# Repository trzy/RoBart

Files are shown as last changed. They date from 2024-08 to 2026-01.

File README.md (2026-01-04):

# RoBart: Autonomous LLM-controlled robot using iPhone
*Copyright 2024-2026 Bart Trzynadlowski*

**What if you could put your brain in a robot body?** Okay, okay, that's not possible, but what if you could put Claude or GPT-4 in a robot body? And not just any robot body but a robot body based on a salvaged hoverboard and an iPhone Pro for compute and sensors? That's exactly what I did. Read on, human!

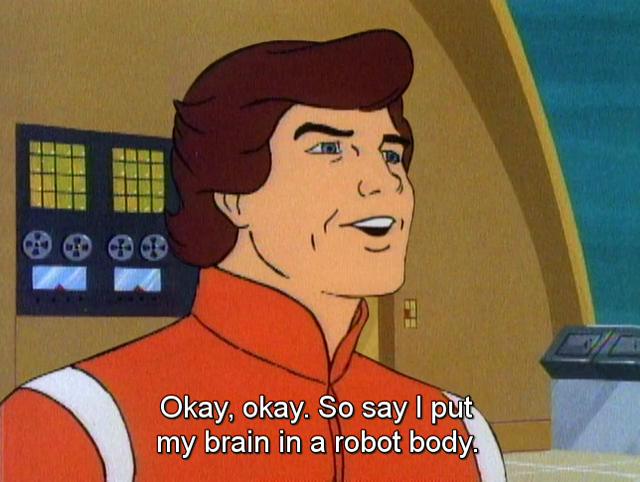
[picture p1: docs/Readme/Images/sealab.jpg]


<table align="center">
  <tr>
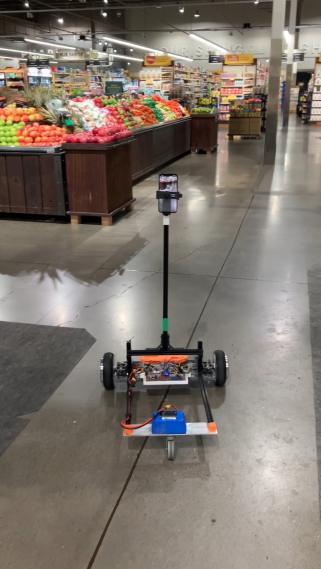
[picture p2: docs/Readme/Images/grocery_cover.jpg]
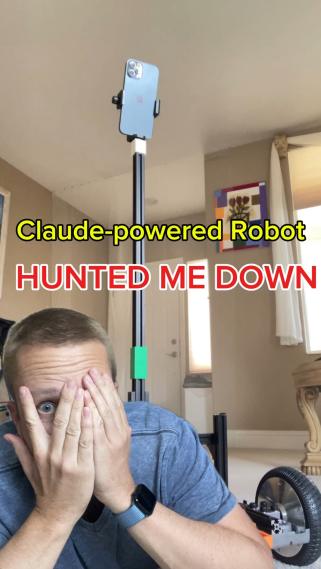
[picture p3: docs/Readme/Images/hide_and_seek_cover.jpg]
    <td align="center"></td> <td align="center"></td>
  </tr>
  <tr>
    <td align="center"><a href="https://www.youtube.com/watch?v=-iW3Vzzr3oU">Grocery shopping</a></td> <td align="center"><a href="https://www.youtube.com/shorts/hnw6pvyZSns">Hide and seek</a></td>
  </tr>
</table>

## Update: January 2026

A teleoperation system using WebRTC and a web client is available for RoBart in [the webrtc-teleop branch](https://github.com/trzy/RoBart/tree/webrtc-teleop).

<table align="center">
  <tr>
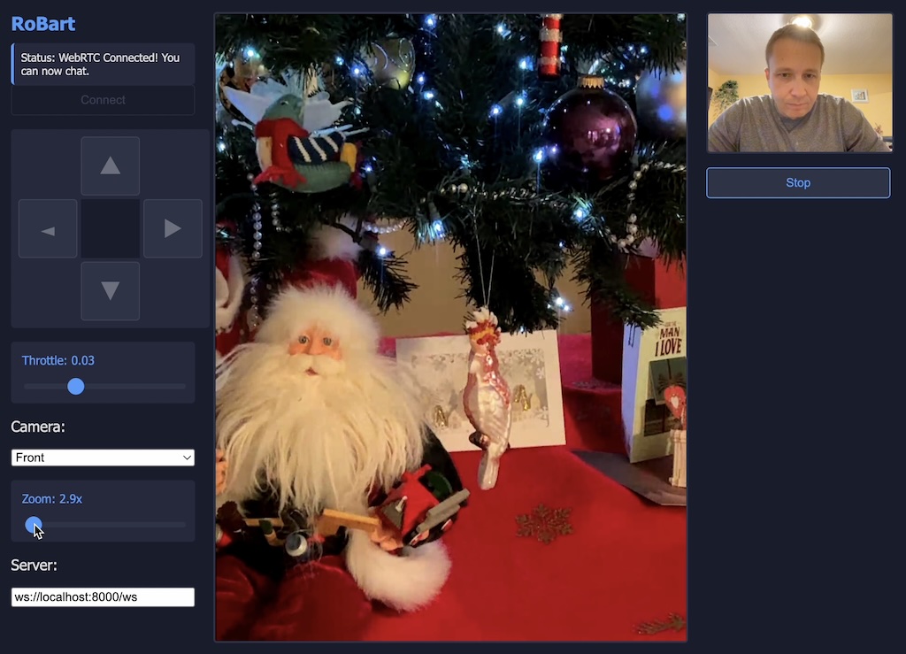
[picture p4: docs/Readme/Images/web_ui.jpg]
    <td align="center"></td>
  </tr>
  <tr>
    <td align="center">Teleoperation interface.</td>
  </tr>
</table>

## Objectives

RoBart began as an attempt to build a cheap mobile base using a hoverboard and iPhone Pro. Mobile phones are easy to work with and provide plenty of compute, connectivity, and useful peripherals: RGB cameras, LiDAR, microphones, speakers. Using [ARKit](https://developer.apple.com/augmented-reality/arkit/), we get SLAM, scene understanding, spatial meshing, and more. Let's see what we can do with this!

I'm open sourcing this project to stimulate discussion and encourage exploration. Some topics to consider:

- **Navigation:** RoBart needs better motion planning and navigation, particularly in household environments. An initial step would be to build a proper [nav mesh](https://en.wikipedia.org/wiki/Navigation_mesh) from its occupancy maps. Proper motion planning would be next.
- **Agent:** The agent could easily be improved with better planning, long-term memory, and spatial awareness. [Vision fine-tuning with GPT-4o](https://openai.com/index/introducing-vision-to-the-fine-tuning-api/) opens up all sorts of exciting possibilities.
- **Mechanical Design:** The mechanical design is a one-off. Can we design a simpler robot that's easier to replicate entirely from off-the-shelf and 3D-printed parts? Virtually nothing would need changing in the code.
- **Manipulation:** A RoBart Mk II should include an end effector, maybe something like this [5-dof Waveshare arm](https://www.waveshare.com/roarm-m1.htm) or the [SO-ARM100](https://github.com/TheRobotStudio/SO-ARM100).
- **Applications:** Accessibility? Tidying-up? Contactless health? Home inspection and security? A robotic porter? What are some fun ideas that could be built?

If you have ideas or contributions, I encourage you to reach out!

<table align="center">
  <tr>
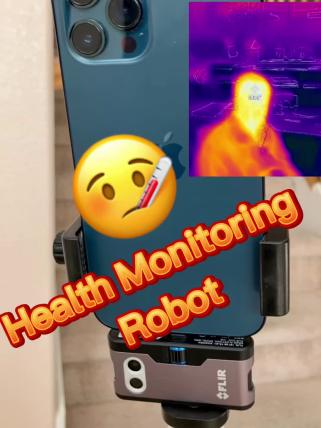
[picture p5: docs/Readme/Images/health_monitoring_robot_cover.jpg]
    <td align="center"></td>
  </tr>
  <tr>
    <td align="center"><a href="https://youtube.com/shorts/GWkYCer5hi8">Contactless health monitoring.</a> Source code for this prototype is not included in this repo.</td>
  </tr>
</table>

## System Architecture

RoBart is a bit of a fever dream of ideas, many only partly finished. I'll attempt to describe how the code base works here.

### High-Level Overview

The RoBart code base contains four distinct applications, only two of which constitute the robot:

1. **iOS application:** This is the main RoBart app that runs on iPhone and controls RoBart. It does not rely on a companion server and makes calls to public LLM APIs directly. The app actually has two modes: robot and handheld, the latter localizing itself to the same SLAM map and allowing for remote control. Located in `ios/RoBart/`.
2. **Arduino firmware:** Firmware that runs on the [Adafruit Feather nRF52 Bluefruit LE](https://www.adafruit.com/product/3406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) to control the motors. Communicates with the iOS app via Bluetooth Low Energy. Located in `hoverboard/`.
3. **watchOS application:** An optional Apple Watch app that allows voice commands to be issued from Watch. This is useful in noisy environments that confound the VAD running on the iPhone. Located in `ios/RoBart/RoBart Remote Control Watch App/` as a watchOS build target.
4. **Debug server:** A Python-based server that the iOS app will attempt to connect to. Provides an interactive terminal that allows various debug commands to be issued, both to control the robot and request data from it. This is not required to operate the robot. Located in `server/`.

The main components of the RoBart iOS app are shown in the diagram below.

<table align="center">
  <tr>
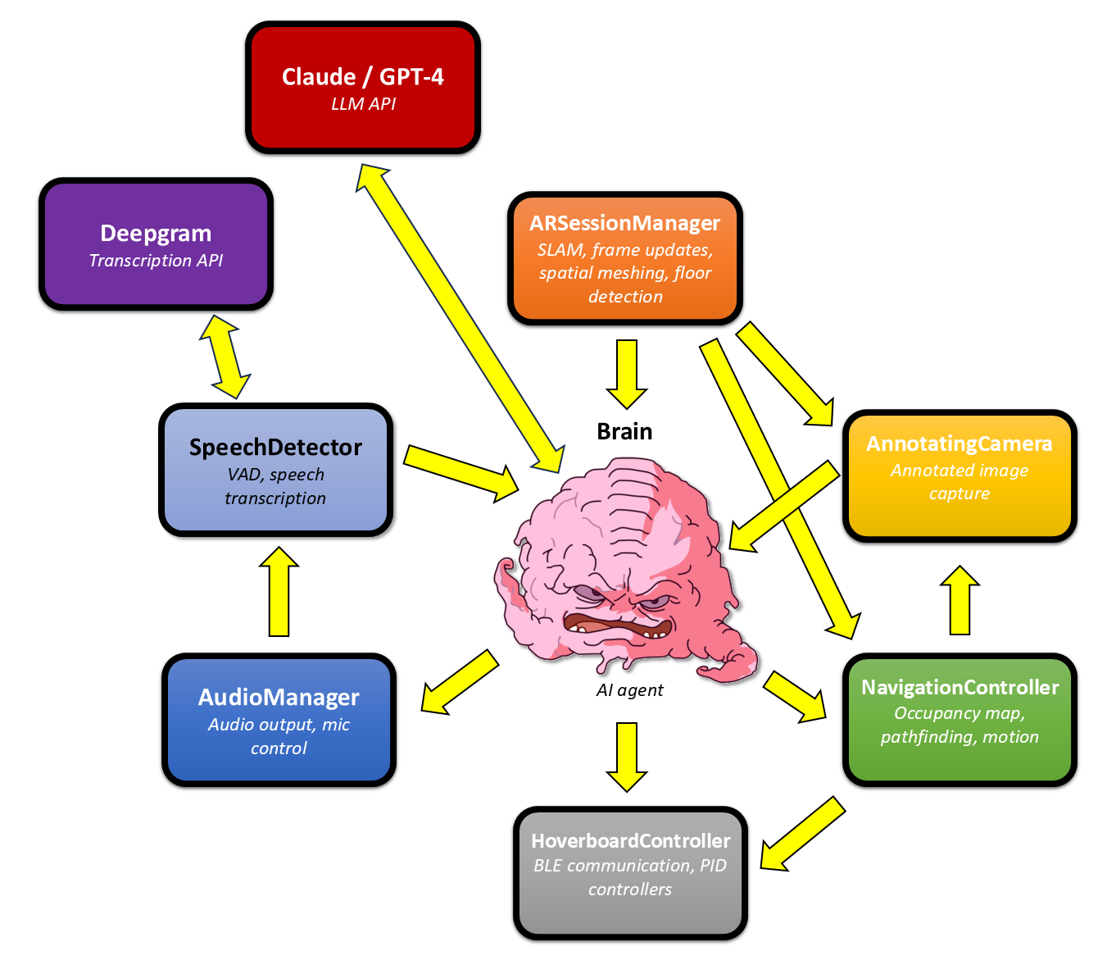
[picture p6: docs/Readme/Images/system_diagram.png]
    <td align="center"></td>
  </tr>
  <tr>
    <td align="center">RoBart iOS app architecture.</td>
  </tr>
</table>

The components are:

- **ARSessionManager:** Using ARKit, publishes camera transform and frame updates, performs scene meshing and floor plane detection, and even supports collaborative sessions with other phones running the app in handheld mode. RoBart components frequently poll the current camera transform or wait for the next frame.
- **SpeechDetector:** Listens for spoken audio, transcribes it using Deepgram, and then publishes the resulting transcript. An external transcription API is used because iOS's `SFSpeechRecognizer` is performance intensive.
- **AudioManager:** Plays audio samples (i.e., RoBart's spoken utterances) and controls the microphone (used by `SpeechDetector`).
- **HoverboardController:** Executes trajectories (e.g., rotate N degrees, drive forward N meters) using PID control on iOS and by sending motor throttle commands to the hoverboard Arduino firmware via BLE.
- **NavigationController:** Higher-level motion control and navigation. Builds an occupancy map, performs very crude pathfinding, provides a nearest-human following task, and executes motion tasks using `HoverboardController`.
- **AnnotatingCamera:** Takes photos and annotates them with navigable points (using the occupancy map). This allows the AI agent to reason about where it can move.
- **Brain:** The AI agent that runs RoBart. Listens for speech and will then attempt to complete the requested task using all of RoBart's capabilities and the chosen LLM.

### Motor Control

`HoverboardController` communicates with the Arduino firmware via BLE. It sends individual motor throttle values (ranging from -1.0 to +1.0, with sign indicating direction) directly. A number of basic trajectory commands are handled on iOS by employing a PID controller that uses ARKit's 6dof pose for feedback (yes, running a PID loop like this through BLE and with ARKit's latency is engineering malpractice but it almost works). These include:

- **drive:** Sets the individual throttle values for the left and right motors, open loop.
- **rotateInPlace:** Turns in place with the given angular velocity (-1 being left at full throttle and +1 being right at full throttle), open loop.
- **rotateInPlaceBy:** Rotates in place by a specified number of degrees.
- **face:** Turns in place to face the given world space direction vector.
- **driveForward:** Drive forward by the specified distance in meters.
- **driveTo:** Drives to the specified world space position in a straight line, both turning to face the point and moving towards it.
- **driveToFacing:** Drives to the specified position while facing the given direction. Particularly useful for driving backwards to a point.

<table align="center">
  <tr>
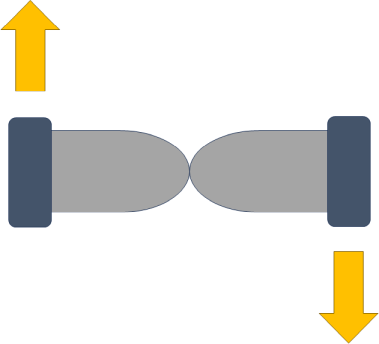
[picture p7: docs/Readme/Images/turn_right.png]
    <td align="center"></td>
  </tr>
  <tr>
    <td align="center">Schematic top-down view of the hoverboard. Rotating right can be accomplished with multiple commands, e.g., <b>drive(leftThrottle: 1, rightThrottle: -1)</b>.</td>
  </tr>
</table>

There is currently no feedback on the Arduino side. No encoder is present on the motors. A watchdog mechanism exists that will cut motor power when either the BLE connection is lost or if motor throttle values are not updated within a certain number of seconds. In the PID controlled modes, a stream of constant updates is sent, which prevents the watchdog from engaging. 

### Position Tracking and Mapping with ARKit

[ARKit](https://developer.apple.com/augmented-reality/arkit/) provides [SLAM](https://en.wikipedia.org/wiki/Simultaneous_localization_and_mapping) for 6dof position and a slew of other useful perception capabilities. The `ARSessionManager` singleton, found in `ios/RoBart/RoBart/AR/ARSessionManager.swift`,
handles the AR session and exposes various useful properties. [RealityKit](https://developer.apple.com/documentation/realitykit) is used for debug rendering of meshes and planes. The AR session is initiated from the AR view container in `ios/RoBart/RoBart/Views/AR/ARViewContainer.swift`

For collision avoidance, RoBart constructs an occupancy map. This is a regular 2D grid on the xz-plane indicating cells that contain world geometry. It is computed by taking all of the vertices produced by scene meshing (see [`ARMeshAnchor`](https://developer.apple.com/documentation/arkit/armeshanchor)) and using a [Metal](https://developer.apple.com/metal/) compute shader to project them onto a 2D grid. The resulting map is used to test for obstructions and plot paths. The occupancy map code is found in `ios/RoBart/RoBart/Navigation/Mapping/`. In order to build it, RoBart needs to know the floor height (i.e., its world space y component) because the occupancy map is computed by looking for obstacles that are within a certain height range above the floor.

<table align="center">
  <tr>
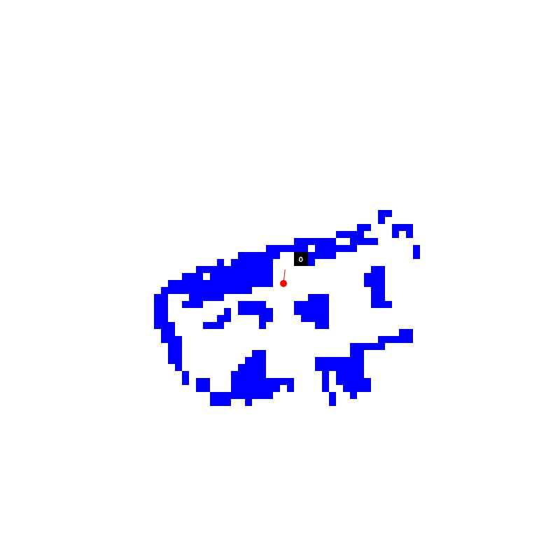
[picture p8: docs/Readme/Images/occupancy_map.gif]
    <td align="center"></td>
  </tr>
  <tr>
    <td align="center">Occupancy map and paths as RoBart explores my house.</td>
  </tr>
</table>

### Photo Input

<table align="center">
  <tr>
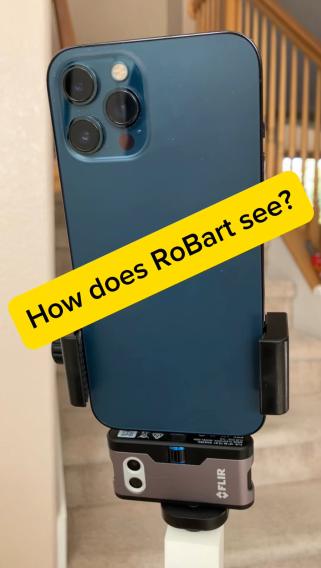
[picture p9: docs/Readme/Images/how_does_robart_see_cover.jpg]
    <td align="center"></td>
  </tr>
  <tr>
    <td align="center"><a href="https://www.youtube.com/shorts/68BlqNpVZNE">How does RoBart see?</a> A video explaining how photos are used in conjunction with the navigation system.</td>
  </tr>
</table>

`AnnotatingCamera` takes photos captured by ARKit (which include the camera pose and camera intrinsics) and annotates them with *navigable points*. This is performed by first placing a series of fixed points on the floor (recall that the floor elevation is provided by `ARSessionManager`) in 3D space near the robot and then determining which of these are *navigable*. That is, points reachable from the current position without obstruction, as indicated by the occupancy map. Finally, the navigable points are projected onto the 2D photo using the camera intrinsics and rendered as numbers atop black rectangles on the image. These annotated images allow the LLM to generate specific instructions for navigation.

<table align="center">
  <tr>
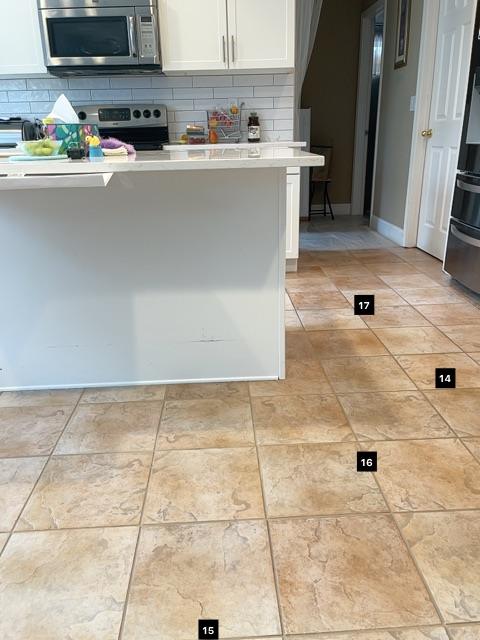
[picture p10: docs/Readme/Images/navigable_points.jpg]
    <td align="center"></td>
  </tr>
  <tr>
    <td align="center">Navigable points in the kitchen.</td>
  </tr>
</table>

### Voice Input

Two methods of voice input are provided:

1. The iOS app can listen directly to the microphone. The WebRTC VAD (voice activity detector) is used to detect human speech. Speech is uploaded to [Deepgram](https://www.deepgram.com) for transcription. An API key must be provided in the settings view. The built-in `SFSpeechRecognizer` could have been used but given how intensively ARKit is used, it would add even more computational load. The big drawback of the current system, however, is that the VAD is not very good, especially in noisy settings.
2. A Watch app target is provided that allows Apple Watch to be used as a microphone. Audio is streamed to the iOS app seamlessly via [Watch Connectivity](https://developer.apple.com/documentation/watchconnectivity). Because recording is manually started and stopped, this is much more reliable and I frequently use this when giving demos of RoBart outside the home.

### Agent Loop

RoBart uses a very simple ReAct-like (reason and act) prompting method for its agent. A great overview of ReAct prompting [exists here](https://github.com/williamcotton/empirical-philosophy/blob/main/articles/how-react-prompting-works.md). Rather than merely interleaving *thought* and *observation* sections, a number of specialized sections are generated using XML tags. A parser parses these into `ThoughtRepresentable` objects (all of this code is in `ios/RoBart/RoBart/Brain/`), which can later be serialized back into the message format expected by the LLM (OpenAI's and Anthropic's APIs differ). Having a parsed list of objects makes it easy to programmatically insert sections and prune the context by discarding old ones. To illustrate exactly how the agent works, I asked RoBart to "look directly behind you and describe what you see." Below is the complete message sequence sent to Claude. This particular example involved five steps:

1. The transcribed speech was wrapped in a `<HUMAN_INPUT>` section along with a photo from that moment and sent to Claude.
2. As per its system instructions, the agent responded with `<PLAN>`, `<MEMORY>` (initially empty), `<INTERMEDIATE_RESPONSE>`, and finally, `<ACTIONS>` containing actions to perform.
3. The two actions were executed in sequence: turn 180 degrees, take photo.
4. An `<OBSERVATIONS>` section was appended and sent to Claude. This contains the photo taken by the `takePhoto` command as well as some textual information about how RoBart moved and its final position.
5. The agent responded with `<FINAL_RESPONSE>` because the task was completed successfully.

```
<HUMAN_INPUT>look directly behind you and describe what you see
photo0: <image>
</HUMAN_INPUT>

<PLAN>
- Long-term plan: Turn 180 degrees to look behind current position and describe what's there
- Current observations: I am currently facing some area but need to turn to see behind
- Sub-problem: Execute a simple turn and take a photo
- Progress: Haven't started yet but straightforward task
- Information needed: Just a photo of what's behind current position
- Capabilities to use: turnInPlace and takePhoto
- Steps:
  1. Turn 180 degrees
  2. Take a photo
  3. Describe what I see
</PLAN>

<MEMORY>
[]
</MEMORY>

<INTERMEDIATE_RESPONSE>
I will turn around to look behind me.
</INTERMEDIATE_RESPONSE>

<ACTIONS>
[
    {"type": "turnInPlace", "degrees": 180},
    {"type": "takePhoto"}
]
</ACTIONS>

<OBSERVATIONS>Turned -175.16881 degrees
Took photo photo1
Current position: (x=0.10 meters,y=0.11 meters)
Current heading: 6 deg
Current view, photo1 taken during last actions step: <image>
</OBSERVATIONS>

<FINAL_RESPONSE>I see a music area with a keyboard, a speaker mounted on the wall, a chair, and some storage containers against a yellow wall with a decorative border.</FINAL_RESPONSE>
```

## Mechanical and Electrical Design

<table align="center">
  <tr>
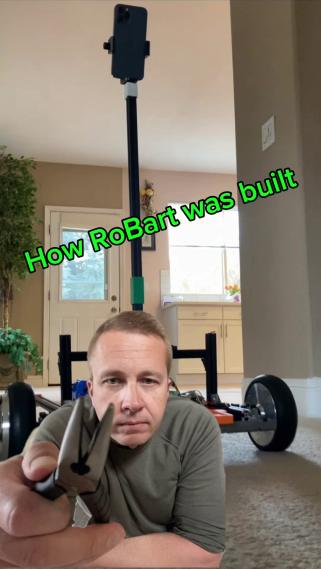
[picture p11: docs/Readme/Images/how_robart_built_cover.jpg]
    <td align="center"></td>
  </tr>
  <tr>
    <td align="center"><a href="https://www.youtube.com/watch?v=M3eoZ8f6cRU">How RoBart is constructed.</a> A video explaining the physical construction.</td>
  </tr>
</table>

The RoBart iOS code is only very weakly dependent on the actual physical form factor of the robot. It would be trivial to build a very different mobile platform. Here, I'll loosely describe the platform I use (which I received some invaluable help from a friend at [BridgeWire](https://bridgewire.org/)).

RoBart is based on the [Hover-1 H1](https://www.amazon.com/Hover-1-Electric-Balancing-Hoverboard-Scooter/dp/B0DJQ6996R) with plastic shell and original electronics removed. Aluminum extrusions (2020) are used to create a frame to which a rear caster and the iPhone are attached. 

The hoverboard motors are controlled by an [Adafruit Feather nRF52 Bluefruit LE](https://www.adafruit.com/product/3406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), which communicates wirelessly via BLE with the iPhone. A [DC-DC converter](https://www.amazon.com/gp/product/B0B7MG2TSB/ref=ppx_yo_dt_b_search_asin_title?ie=UTF8&psc=1) steps down the 36V battery voltage to the 3.3V required by the Feather board. Two [RioRand 350W](https://www.amazon.com/RioRand-6-60V-Brushless-Electric-Controller/dp/B087M2378D) brushless DC motor drivers are used to drive the hoverboard motors. The appropriate connectors will be necessary -- I believe I used [these](https://www.amazon.com/dp/B083GQHG5R?ref=ppx_yo2ov_dt_b_fed_asin_title&th=1) and [these](https://www.amazon.com/dp/B09DTL4T1W?ref=ppx_yo2ov_dt_b_fed_asin_title) to connect the motors to the driver boards, [Dupont connectors](https://www.amazon.com/dp/B0CL9L3W68?ref=ppx_yo2ov_dt_b_fed_asin_title) to connect the driver boards to the Feather, and various XT60 splitter cables for routing battery power.

There is a 3D-printed mount for the phone holder atop the vertical extrusion. The extrusion itself has been cut and joined with a removable plastic connector in order to allow RoBart to be transported in the trunk of a car. STL files for all 3D printed parts are available in `parts/`, including a case that houses one of the original Hover-1 H1 logic boards to use as a battery charger.

## License

RoBart is distributed as free software under the terms of the GNU General Public License (Version 3), included [here](LICENSE).

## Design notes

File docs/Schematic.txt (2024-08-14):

Board Layout
============

  +-------------------------------------+        +--------+        +-------------------------------------+
  |           LEFT MOTOR BOARD          |        |Feather |        |   . . . . .    . . . . .            |
  |                                    o|        |        |        |      Hall      G P V S G            |
  |o Phase A                           o|        |        |        |o Stop                          Gnd o|
  |o Phase B                       Gnd o|        |        |        |o Brake                         Vdd o|
  |o Phase C                       Dir o|        |        |        |o Dir                       Phase C o|
  |o Vdd                         Brake o|        |        |        |o Gnd                       Phase B o|
  |o Gnd                          Stop o|        |        |        |o                           Phase A o|
  |            G S V P G      Hall      |        |        |        |o                                    |
  |            . . . . .    . . . . .   |        |        |        |                                     |
  +-------------------------------------+        +--------+        +-------------------------------------+

      +-----------------------------+                                     +---------------------------+
      |o Vin+                Vout+ o|                                     |                    ooo    |
      |                      (3.3V) |                                     |  Distribution  Gnd ooo    |
      |   Voltage Regulator         |                                     |                    ooo    |
      |                             |                                     +---------------------------+
      |o Vin-                Vout- o|                                     |                     oo    |
      +-----------------------------+                                     |                Vcc  oo    |
                                                                          |                     oo    |
                                                                          +---------------------------+

Wiring:

  Left motor is wired to inputs on left motor board (screw terminals on the RioRand 350W).
  Right motor is wires to inputs on right motor board. Note: the right RioRand board is upside down.

                    /
                   | Phase A (Left Motor Board)
    Left Motor ->  | Phase B
                   | Phase C
                    \

                    /
                   | Phase A (Right Motor Board)
    Right Motor -> | Phase B
                   | Phase C
                    \

  Vdd and Gnd on both left and right boards connects to battery Vdd and Gnd.

  Control terminal of left motor board (right side of left motor board, above) is wired to the left
  side of the Feather board:

    Left Motor Board Gnd    -> Distribution Board Gnd
    Left Motor Board Dir    -> A0 (below GND; the 5th pin from top left reset pin)
    Left Motor Board Brake  -> A1 (below A0)
    Left Motor Board Stop   -> A2 (below A1)

  PWM signal (P pin of GSVPG connector at the bottom of the motor board) connects to the Feather
  board:

    Left Motor Board PWM    -> A3 (below A2)

  Control terminal of right motor board is wired to the right side of the Feather board:

    Right Motor Board Gnd   -> Distribution Board Gnd
    Right Motor Board Dir   -> Pin 11 (P0.11)
    Right Motor Board Brake -> Pin 7 (P0.07)
    Right Motor Board Stop  -> Pin 15 (P0.15)

  PWM signal:

    Right Motor Board PWM   -> Pin 16 (P0.16, below USB POWER / VBUS pin)

  Feather board power and grounding:

    Feather GND   -> Distribution Board Gnd
    Feather VBAT  -> Distribution Board Vcc

  Voltage regulator:

    Battery Vdd   -> Vin+
    Battery Gnd   -> Vin-
    Vout+         -> Distribution Board Vcc
    Vout-         -> Distribution Board Gnd

  The distribution board serves to act as Vcc and Gnd nodes for all logic, at
  3.3V. It serves the Feather board (VBAT and GND) as well as the motor control
  boards (Gnd).

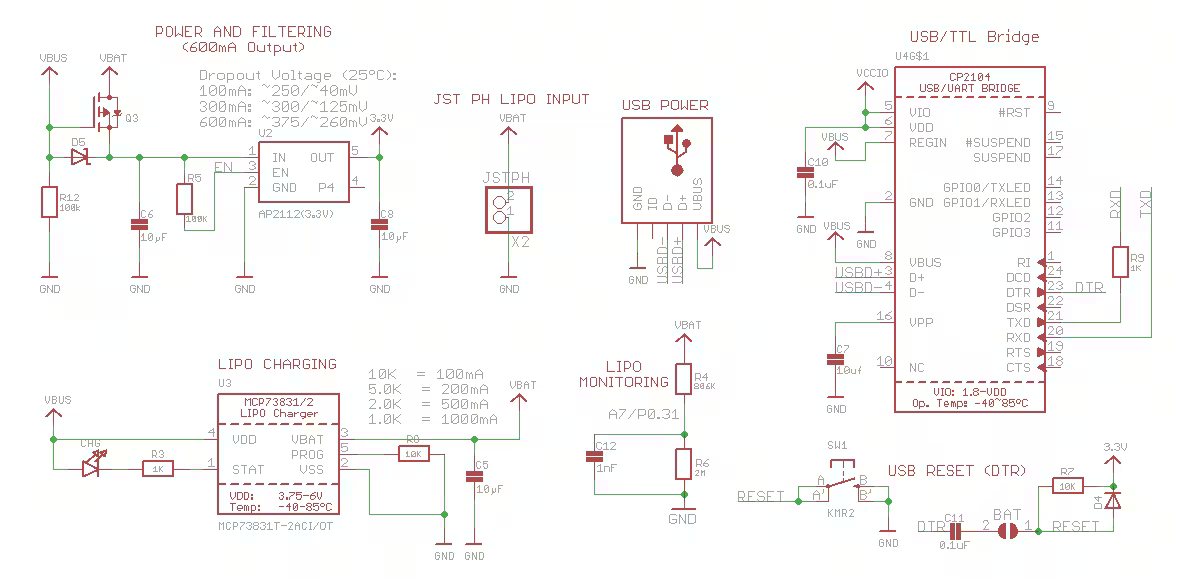
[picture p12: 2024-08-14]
docs/Feather nRF52832/nRF52 Bluefruit LE Feather - Schematic2.png

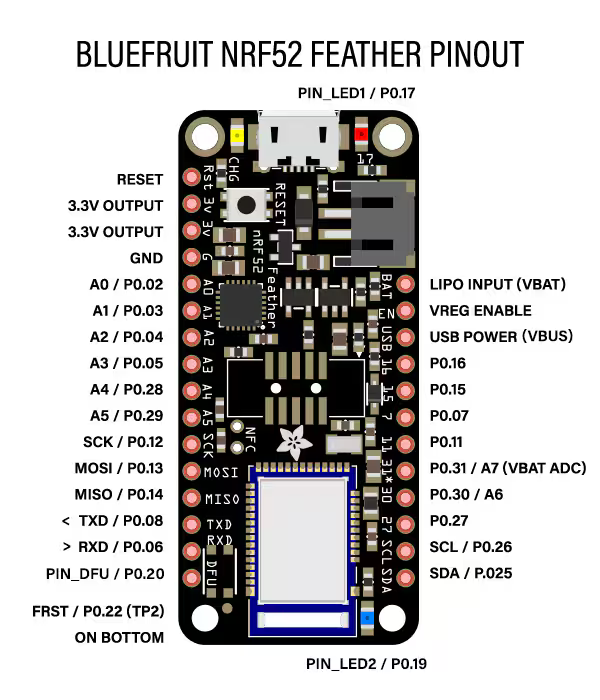
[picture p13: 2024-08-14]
docs/Feather nRF52832/nRF52 Bluefruit LE Feather - Pinout.png

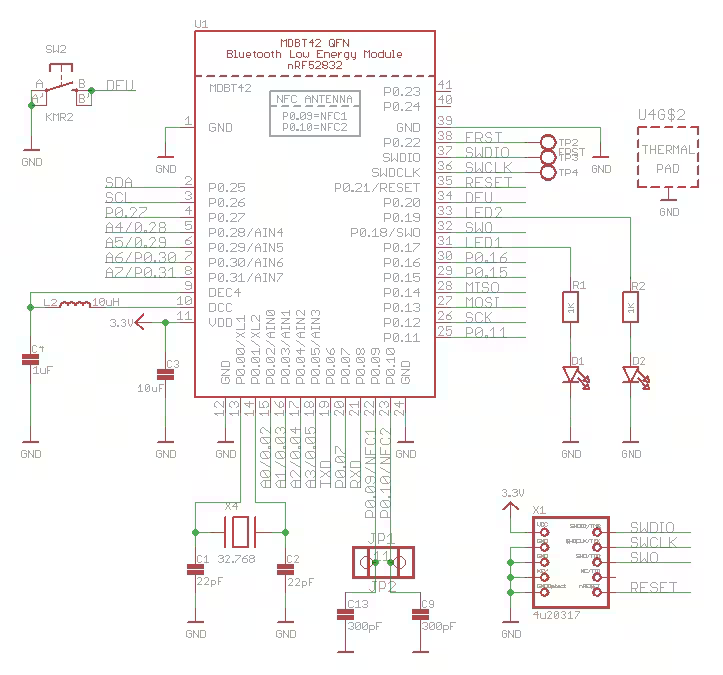
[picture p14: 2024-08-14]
docs/Feather nRF52832/nRF52 Bluefruit LE Feather - Schematic1.png

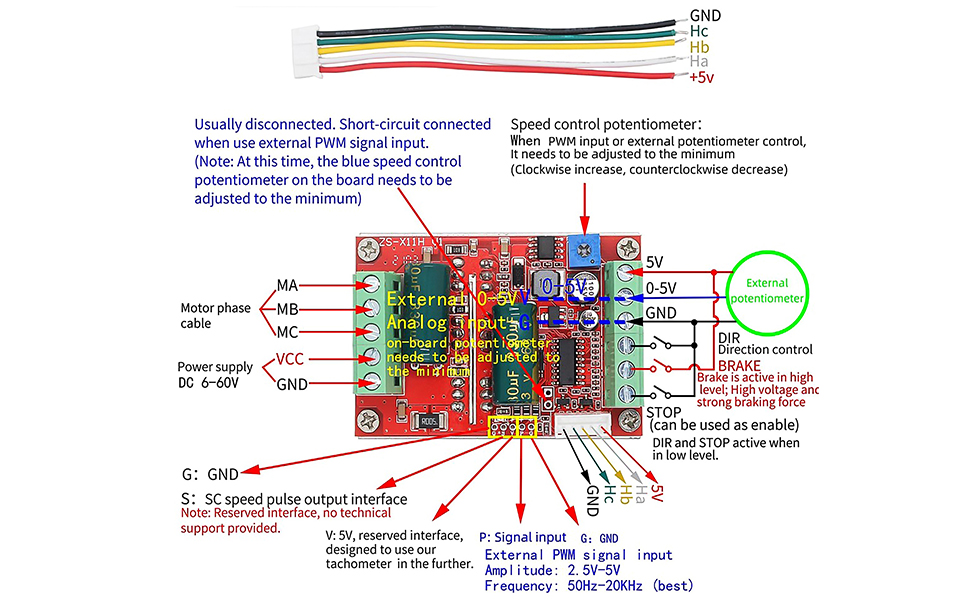
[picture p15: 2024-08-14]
docs/RioRand 350W/pins.jpg

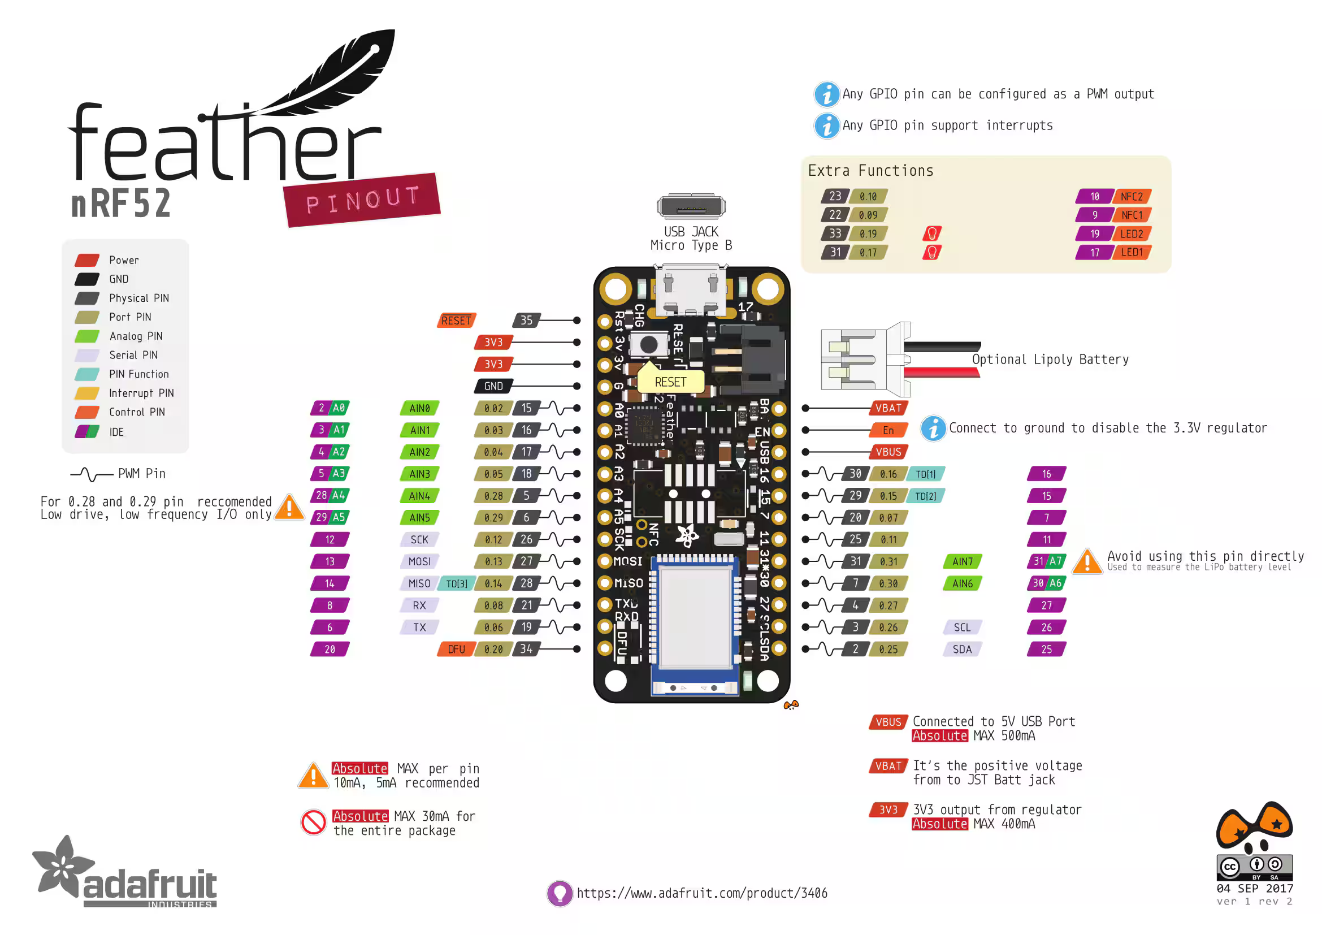
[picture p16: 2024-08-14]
docs/Feather nRF52832/nRF52 Bluefruit LE Feather - Pin Function.png

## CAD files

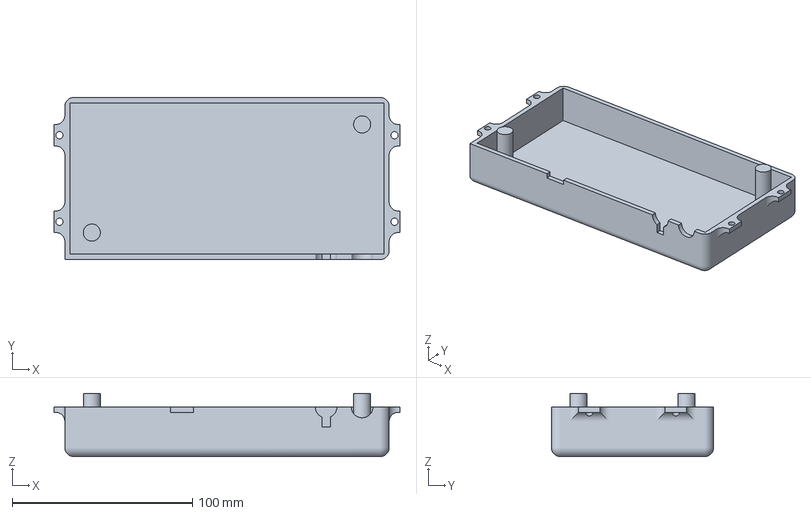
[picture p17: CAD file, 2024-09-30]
parts/Case Top.3mf
192.0 x 90.0 x 35.0 mm

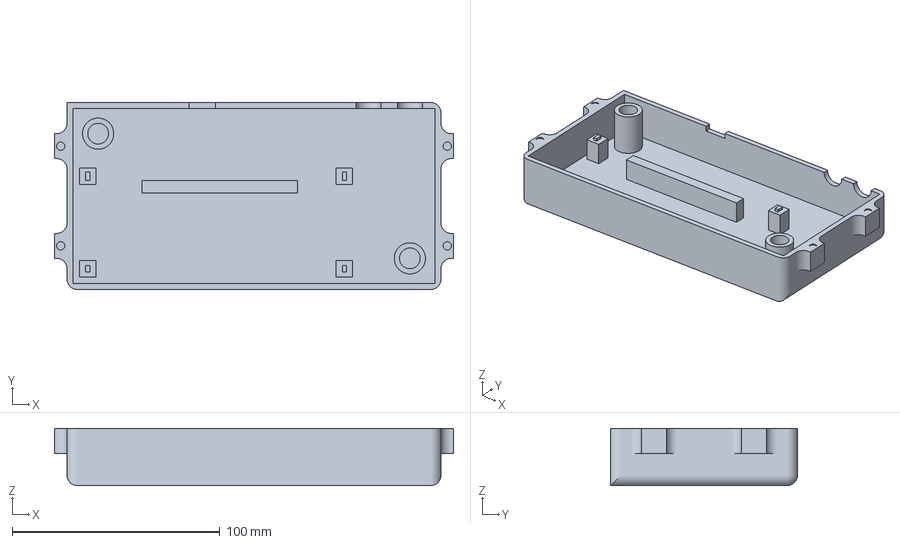
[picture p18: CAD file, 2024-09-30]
parts/Case Bottom.3mf
192.0 x 90.0 x 27.5 mm

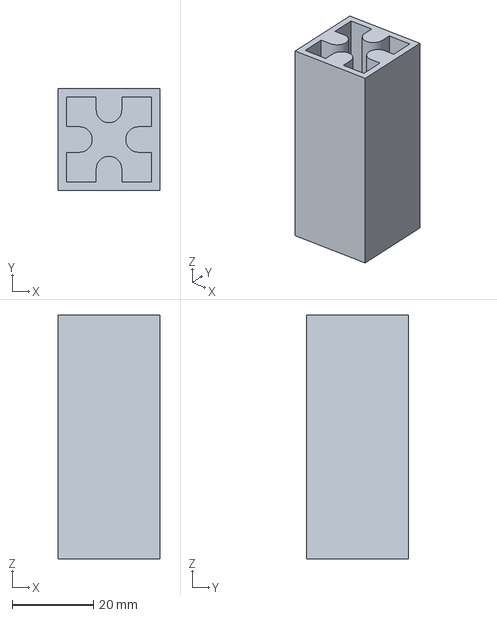
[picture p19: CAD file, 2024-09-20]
parts/Extrusion Connector.3mf
25.0 x 25.0 x 60.0 mm

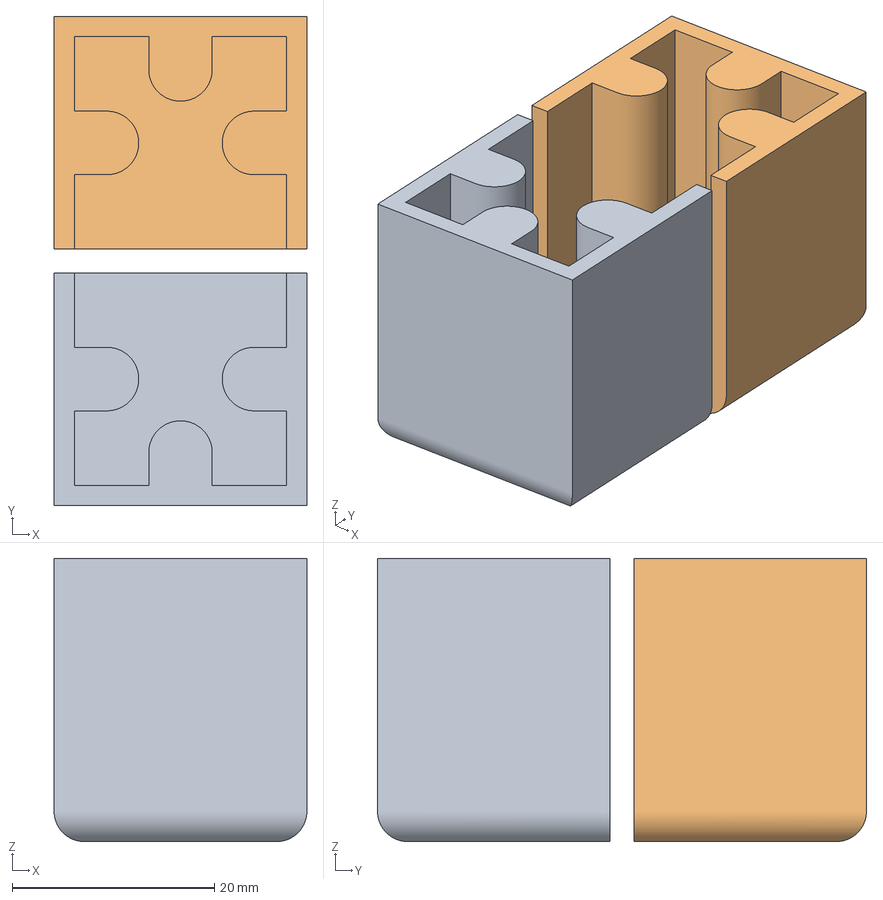
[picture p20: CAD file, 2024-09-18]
parts/Extrusion Horizontal End Caps.3mf
25.0 x 48.3 x 28.0 mm
Extrusion Horizontal End Cap.stl x 2

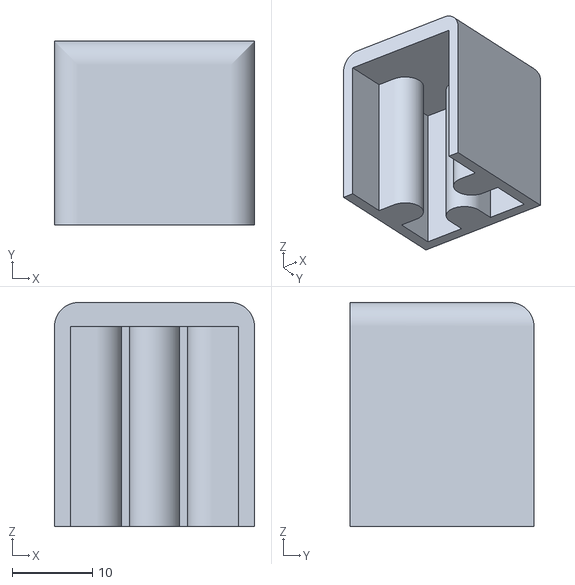
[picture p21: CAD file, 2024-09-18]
parts/Extrusion Horizontal End Cap.stl
25.0 x 23.0 x 28.0

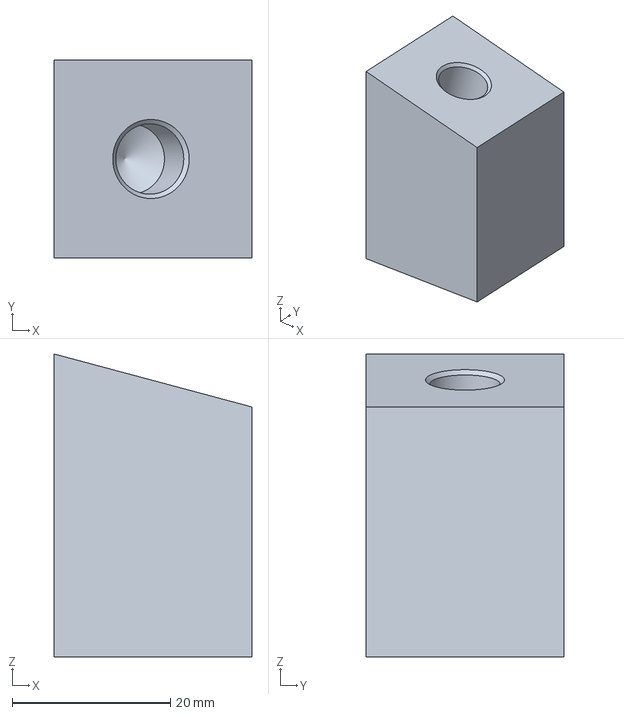
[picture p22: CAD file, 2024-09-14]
parts/Camera Mount - 15 Degrees.3mf
25.0 x 25.0 x 38.3 mm

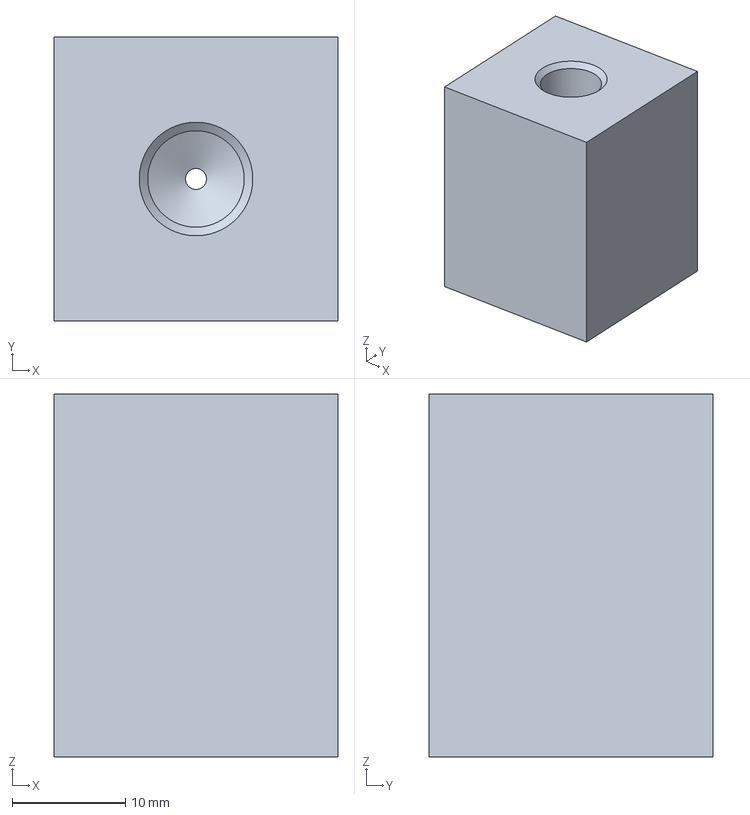
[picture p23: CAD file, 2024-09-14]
parts/Camera Mount - 0 Degrees.3mf
25.0 x 25.0 x 32.0 mm

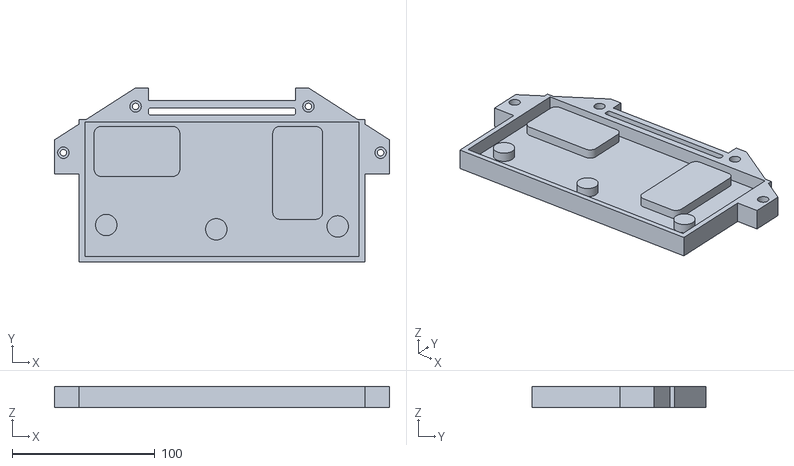
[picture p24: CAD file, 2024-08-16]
parts/Hoverboard Circuit Board Mounting Plate - Front Mount - USB Inwards.stl
234.5 x 122.0 x 15.0

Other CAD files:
parts/Hoverboard Circuit Board Mounting Plate - Front Mount - USB Outwards.stl
parts/Camera Mount - 0 Degrees.stl
parts/Camera Mount - 15 Degrees.stl
parts/Case Bottom.stl
parts/Case Top.stl
parts/Extrusion Connector.stl

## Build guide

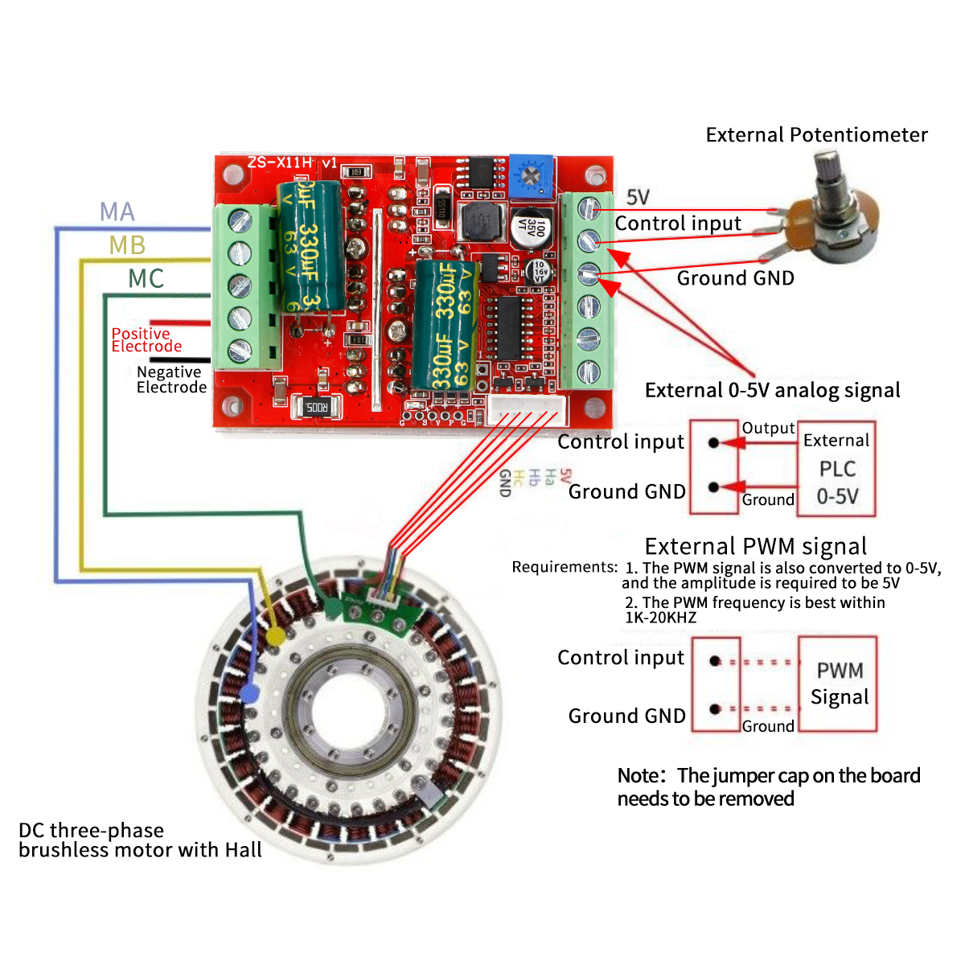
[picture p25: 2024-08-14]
docs/RioRand 350W/operation.jpg

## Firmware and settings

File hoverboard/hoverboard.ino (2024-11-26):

/*
 * hoverboard.ino
 * RoBart
 * Bart Trzynadlowski, 2024
 *
 * Hoverboard controller for Adafruit Feather nRF52832 board. Listens for commands from iOS via
 * Bluetooth and drives two RioRand 350W BLDC motor controllers.
 *
 * This file is part of RoBart.
 *
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
 * You should have received a copy of the GNU General Public License along
 * with RoBart. If not, see <http://www.gnu.org/licenses/>.
 */

#include "nRF52_PWM.h"  // nrF52_PWM package
#include "messages.hpp"
#include "cooperative_task.hpp"
#include "bluetooth.hpp"
#include <algorithm>
#include <cmath>
#include <limits>


/***************************************************************************************************
 Motor Control
***************************************************************************************************/

constexpr uint32_t PIN_LEFT_DIR = 2;    // pin A0
constexpr uint32_t PIN_LEFT_BRAKE = 3;  // pin A1
constexpr uint32_t PIN_LEFT_STOP = 4;   // pin A2
constexpr uint32_t PIN_LEFT_PWM = 5;    // pin A3

constexpr uint32_t PIN_RIGHT_DIR = 11;  // pin 11
constexpr uint32_t PIN_RIGHT_BRAKE = 7; // pin 7
constexpr uint32_t PIN_RIGHT_STOP = 15; // pin 15
constexpr uint32_t PIN_RIGHT_PWM = 16;  // pin 16

static float s_pwm_frequency = 20000.0f;
static nRF52_PWM *s_pwm_left = nullptr;
static nRF52_PWM *s_pwm_right = nullptr;


enum MotorSide
{
  Left,
  Right
};

/*
 * Sets motor speed.
 *
 * Parameters:
 *  motor:      Which motor: Left or Right.
 *  magnitude:  0 (stopped) to 1.0 (full speed in currently-set direction).
 */
static void speed(MotorSide motor, float magnitude)
{
  // Compute duty cycle ticks: [0%,100%] -> [0,65535] (cannot use setPWM() because it erroneously
  // casts to an integer before remapping, making it impossible to specify < 1%)
  magnitude = max(0.0f, min(1.0f, magnitude));
  const uint16_t duty_cycle = uint16_t(round(magnitude * 65535.0f));

  if (motor == Left)
  {
    s_pwm_left->setPWM_Int(PIN_LEFT_PWM, s_pwm_frequency, duty_cycle);
  }
  else
  {
    s_pwm_right->setPWM_Int(PIN_RIGHT_PWM, s_pwm_frequency, duty_cycle);
  }
}

/*
 * Sets motor direction. Forward is the same for both motors. That is, the necessary adjustment is
 * made to the right motor, which is wired such that forward on the RioRand board is actually
 * backwards unless corrected.
 *
 * Parameters:
 *  motor:    Which motor: Left or Right.
 *  forward:  Spin in forward direction if true, otherwise reverse.
 */
static void direction(MotorSide motor, bool forward)
{
  if (motor == Right)
  {
    // Correct right motor orientation
    forward = !forward;
  }

  uint32_t pin = motor == Left ? PIN_LEFT_DIR : PIN_RIGHT_DIR;
  if (forward)
  {
    // Forward
    pinMode(pin, INPUT);
  }
  else
  {
    pinMode(pin, OUTPUT);
    digitalWrite(pin, LOW);
  }
}

/*
 * Brakes the motor (using active braking, which will bring it to a sudden and possibly violent
 * stop). Use with care.
 *
 * Parameters:
 *  motor:  Which motor: Left or Right.
 *  active: True to apply brake.
 */
static void brake(MotorSide motor, bool active)
{
  uint32_t pin = motor == Left ? PIN_LEFT_BRAKE : PIN_RIGHT_BRAKE;
  if (active)
  {
    // Apply brake
    digitalWrite(pin, HIGH);
  }
  else
  {
    digitalWrite(pin, LOW);
  }
}

/*
 * Stops the motor, removing power and letting it coast.
 *
 * Parameters:
 *  motor:  Which motor: Left or right.
 *  active: True to stop.
 */
static void stop(MotorSide motor, bool active)
{
  uint32_t pin = motor == Left ? PIN_LEFT_STOP : PIN_RIGHT_STOP;
  if (active)
  {
    // Stop motor (coast to stop)
    pinMode(pin, OUTPUT);
    digitalWrite(pin, LOW);
  }
  else
  {
    // High impedance state to deassert STOP
    pinMode(pin, INPUT);
  }
}

static void cut_motor_power()
{
  speed(Left, 0.0f);
  speed(Right, 0.0f);
  stop(Left, true);
  stop(Right, true);
  brake(Left, false);
  brake(Right, false);
}

static void init_motors()
{
  pinMode(PIN_LEFT_PWM, OUTPUT);
  pinMode(PIN_RIGHT_PWM, OUTPUT);
  s_pwm_left = new nRF52_PWM(PIN_LEFT_PWM, s_pwm_frequency, 0.0f);    // 0 duty cycle: off
  s_pwm_right = new nRF52_PWM(PIN_RIGHT_PWM, s_pwm_frequency, 0.0f);  // 0 duty cycle: off
  speed(Left, 0.0f);
  speed(Right, 0.0f);

  pinMode(PIN_LEFT_DIR, OUTPUT);
  pinMode(PIN_RIGHT_DIR, OUTPUT);
  direction(Left, true);
  direction(Right, true);

  pinMode(PIN_LEFT_BRAKE, OUTPUT);
  pinMode(PIN_RIGHT_BRAKE, OUTPUT);
  brake(Left, false);
  brake(Right, false);

  pinMode(PIN_LEFT_STOP, OUTPUT);
  pinMode(PIN_RIGHT_STOP, OUTPUT);
  stop(Left, false);
  stop(Right, false);
}


/***************************************************************************************************
 Watchdog

 Cut the motors after a certain period of inactivity (i.e., incoming control messages).
***************************************************************************************************/

static bool s_watchdog_enabled = true;
static unsigned long s_watchdog_milliseconds = 2000;
static unsigned long s_watchdog_last_message_received_at = 0;

/*
 * Indicates to the watchdog that the remote side is still actively controlling the hoverboard.
 * Call this whenever a motor control message is received.
 */
static void reset_watchdog_timeout()
{
  s_watchdog_last_message_received_at = millis();
}

static void update_watchdog_settings(const watchdog_message *msg)
{
  s_watchdog_enabled = msg->watchdog_enabled != 0;
  double max_millis = double(std::numeric_limits<unsigned long>::max());
  double millis = std::min(msg->watchdog_seconds * 1e3, max_millis);  // clamp to max
  s_watchdog_milliseconds = (unsigned long) millis;                   // convert to integer
  reset_watchdog_timeout();
  Serial.printf("Watchdog settings updated: enabled=%d, milliseconds=%d\n", s_watchdog_enabled, s_watchdog_milliseconds);
}

/*
 * Checks for watchdog timeout and cuts motor power if necessary. Call this periodically.
 */
static void watchdog_tick()
{
  if (!s_watchdog_enabled)
  {
    return;
  }

  static bool printed_message = false;
  unsigned long now = millis();
  unsigned long millis_since_last_message = now - s_watchdog_last_message_received_at;
  if (millis_since_last_message >= s_watchdog_milliseconds)
  {
    cut_motor_power();
    if (!printed_message)
    {
      Serial.println("Watchdog has cut motor power");
      printed_message = true;
    }
  }
  else
  {
    printed_message = false;
  }
}


/***************************************************************************************************
 Bluetooth Communication
***************************************************************************************************/

static bool s_connected = false;

static void on_peripheral_connect(uint16_t connection_handle)
{
  BLEConnection *connection = Bluefruit.Connection(connection_handle);
  char central_name[32] = { 0 };
  connection->getPeerName(central_name, sizeof(central_name));
  Serial.printf("Connected to %s\n", central_name);
  s_connected = true;
}

static void on_peripheral_disconnect(uint16_t connection_handle, uint8_t reason)
{
  Serial.printf("Disconnected: code 0x%02x\n", reason);
  cut_motor_power();  // stop the motors to prevent a runaway RoBart!
  s_connected = false;
}

static void on_received(uint16_t connection_handle, BLECharacteristic *characteristic, uint8_t *data, uint16_t length)
{
  if (length >= 8)
  {
    uint32_t message_length = *reinterpret_cast<uint32_t *>(&data[0]);
    uint32_t message_id = *reinterpret_cast<uint32_t *>(&data[4]);

    if (message_length != length)
    {
      Serial.printf("Error: Received %d bytes but message header says %d bytes\n", length, message_length);
      return;
    }

    HoverboardMessageID id = HoverboardMessageID(message_id);
    switch (id)
    {
    case PingMessage:
      if (length == sizeof(ping_message))
      {
        const ping_message *msg = reinterpret_cast<const ping_message *>(data);
        const pong_message response_msg(msg->timestamp);
        bluetooth_send(reinterpret_cast<const uint8_t *>(&response_msg), sizeof(response_msg));
      }
      else
      {
        Serial.printf("Error: ping_message has incorrect length (%d)\n", length);
      }
      break;

    case WatchdogMessage:
      if (length == sizeof(watchdog_message))
      {
        const watchdog_message *msg = reinterpret_cast<const watchdog_message *>(data);
        update_watchdog_settings(msg);
      }
      else
      {
        Serial.printf("Error: watchdog_message has incorrect length (%d)\n", length);
      }
      break;

    case PWMMessage:
      if (length == sizeof(pwm_message))
      {
        const pwm_message *msg = reinterpret_cast<const pwm_message *>(data);
        s_pwm_frequency = float(msg->pwm_frequency);
        Serial.printf("PWM frequency: %d Hz\n", msg->pwm_frequency);
      }
      else
      {
        Serial.printf("Error: pwm_message has incorrect length (%d)\n", length);
      }
      break;

    case MotorMessage:
      if (length == sizeof(motor_message))
      {
        const motor_message *msg = reinterpret_cast<const motor_message *>(data);
        const float epsilon = 1e-3f;
        bool left_forward = msg->left_motor_throttle >= 0;
        float left_magnitude = fabs(msg->left_motor_throttle);
        bool left_stopped = left_magnitude < 1e-3f;
        bool right_forward = msg->right_motor_throttle >= 0;
        float right_magnitude = fabs(msg->right_motor_throttle);
        bool right_stopped = right_magnitude < 1e-3f;

        stop(Left, left_stopped);
        stop(Right, right_stopped);
        direction(Left, left_forward);
        direction(Right, right_forward);
        speed(Left, left_magnitude);
        speed(Right, right_magnitude);

        reset_watchdog_timeout();
      }
      else
      {
        Serial.printf("Error: motor_message has incorrect length (%d)\n", length);
      }
      break;

    default:
      // Ignore
      break;
    }
  }
}


/***************************************************************************************************
 Entry Point and Main Loop
***************************************************************************************************/

static util::cooperative_task<util::millisecond::resolution> s_led_blinker;

static void blink_led(util::time::duration<util::microsecond::resolution> delta, size_t count)
{
  // Blink when disconnected
  if (s_connected)
  {
    digitalWrite(LED_BUILTIN, LOW);
    return;
  }
  static const bool sequence[] = { true, false, false };
  bool on = sequence[count % (sizeof(sequence) / sizeof(bool))];
  digitalWrite(LED_BUILTIN, on ? HIGH : LOW);
}

void setup()
{
  init_motors();
  Serial.begin(115200);
  s_led_blinker = util::cooperative_task<util::millisecond::resolution>(util::milliseconds(100), blink_led);
  bluetooth_start(on_peripheral_connect, on_peripheral_disconnect, on_received);
  Serial.println("Setup complete");
}

void loop()
{
  watchdog_tick();
  s_led_blinker.tick();
}

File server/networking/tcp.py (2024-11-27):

#
# tcp.py
# Bart Trzynadlowski
#
# This file is part of RoBart.
#
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

#
# Asynchronous TCP server and client. Designed to be run as asynchronous tasks in an event loop.
#

import asyncio
import time
from typing import Tuple
import uuid

from pydantic import BaseModel

from .message_handling import MessageHandler
from .serialization import serialize


class Session:
    def __init__(self, reader, writer, remote_endpoint, message_handler):
        self.remote_endpoint = remote_endpoint
        self._reader = reader
        self._writer = writer
        self._message_handler = message_handler

    def __del__(self):
        print("Session object destroyed")

    def __str__(self):
        return str(self.remote_endpoint)

    async def send(self, message: BaseModel):
        """
        Sends an object as a JSON-encoded message using our custom framing
        protocol:

        Offset  Length  Description
        ------  ------  -----------
        0       4       Length of entire framed message, as a little-endian 32-
                        bit unsigned integer, including these 4 bytes: N.
        4       N - 4   Payload as encoded by LaserTagJSONEncoder. The length is
                        the length given at offset 0 less 4 bytes (i.e., the JSON
                        payload itself).

        Parameters
        ----------
        message : BaseModel
            A Pydantic BaseModel object that will automatically be serialized before transmission.
        """
        try:
            json_string = serialize(message=message)
            json_bytes = json_string.encode("utf-8")
            total_size = 4 + len(json_bytes)  # size prefix + JSON payload
            message_bytes = (
                int(total_size).to_bytes(length=4, byteorder="little")
                + json_bytes
            )
            self._writer.write(message_bytes)
            #print("Sent %d bytes" % len(message_bytes))
            await self._writer.drain()
        except Exception as e:
            # Connection error, most likely. Nothing we can do but swallow it and
            # hope it will be detected elsewhere. Makes for a more ergonomic API when
            # we don't have to worry about send() blowing up.
            print("Exception caught while trying to send: %s" % e)
        pass

    async def _run(self):
        while True:
            # Read header and payload
            try:
                size_prefix = await self._reader.readexactly(4)
                timestamp = time.time()
                total_size = int.from_bytes(bytes=size_prefix, byteorder="little")
                payload_size = total_size - 4
                if payload_size > 0:
                    payload = await self._reader.readexactly(payload_size)
                    json_string = payload.decode("utf-8")
                    #print("Received %d bytes" % total_size)
                    try:
                        await self._message_handler.handle_message(session=self, json_string=json_string, timestamp=timestamp)
                    except Exception as e:
                        print("Terminating session due to exception from message handler: %s" % e)
                        break
            except ConnectionError as e:
                print("Disconnected from %s: %s" % (self.remote_endpoint, e))
                break
            except Exception as e:
                print("Unexpected error in Session: %s" % e)
                break

        # Helps ensure the connection on the other end sees a disconnect,
        # particularly in cases where the message handler raised an exception above
        await self._close()

    async def _close(self):
        try:
            self._writer.close()
            await self._writer.wait_closed()
        except Exception as e:
            # If the socket was actually disconnected already, ConnectionError occurs
            pass

class Server:
    def __init__(self, port: int, message_handler: MessageHandler):
        self.id = str(uuid.uuid1())
        self._port = port
        self.sessions = []
        self._message_handler = message_handler

    async def _on_client_connect(self, reader, writer):
        # Construct a client object
        socket = writer.get_extra_info("socket")
        if socket == None:
            remote_endpoint = "unknown endpoint"
        else:
            peername = socket.getpeername()
            remote_endpoint = ("%s:%d" % peername[0:2]) if len(peername) >= 2 else None
            remote_endpoint = (remote_endpoint if remote_endpoint is not None else "unknown endpoint")
        print("New connection from %s" % remote_endpoint)
        session = Session(reader=reader, writer=writer, remote_endpoint=remote_endpoint, message_handler=self._message_handler)
        try:
            await self._message_handler.on_connect(session=session)
            self.sessions.append(session)
            await session._run()
            print("Ended session with %s" % remote_endpoint)
            await self._message_handler.on_disconnect(session=session)
        except Exception as e:
            print("Unexpected error from Session or its message handler: %s" % e)
            raise   # rethrow so we don't miss e.g. a task cancelation exception
        finally:
            await session._close()
            self.sessions.remove(session)

    async def run(self):
        try:
            server = await asyncio.start_server(client_connected_cb=self._on_client_connect, host=None, port=self._port)
        except Exception as e:
            print("Error: %s" % e)
            raise
        async with server:
            print("Starting server on port %d..." % self._port)
            await server.serve_forever()
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

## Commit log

2024-08-14 Current motor board schematics
2024-08-16 Circuit board mount STL
    [Hoverboard Circuit Board Mounting Plate - Forward Position.stl]
2024-08-16 Parts: Hoverboard circuit board mount STLs (USB outwards and inwards variants)
    [Hoverboard Circuit Board Mounting Plate - Front Mount - USB Inwards.stl, Hoverboard Circuit Board Mounting Plate - Front Mount - USB Outwards.stl]
2024-08-23 iOS: MotorControl views renamed to HoverboardControl, added RTT test
2024-08-23 Server: Added rtt_test command, which prints Hoverboard<->iOS RTT stats
2024-08-24 Hoverboard: Added watchdog to cut motors if remote stop responding and made LED blink only when disconnected
2024-08-24 Hoverboard: Print watchdog message only on when timeout first expires
2024-08-25 Server: Added throttle and PID gain commands
2024-08-25 Hoverboard: PWM frequency can be changed with pwm_message
2024-08-25 Server: throttle command specifies min and max values, added pwm command
2024-08-25 Hoverboard: Manually compute duty cycle ticks for PWM because of bug in library that truncates floating point values
    [hoverboard.ino]
2024-08-25 Server: Allow PWM frequencies up to 50 KHz
2024-08-25 iOS: Cascade PID controller for orientation (still high error and jerky behavior)
2024-08-26 Modeling: Added angular_velocity.py, which plots and estimates angular velocity vs. steering, and moved requirements.txt to root dir
2024-08-26 iOS: Orientation PID only and mapping desired angular velocites to steering command via measured table
2024-08-26 iOS: Remove angular velocity PID and redundant minThrottle setting
2024-08-26 Server: Remove minThrottle from throttle command and remove angular velocity PID settings
2024-08-26 iOS: Reset PID state when gains are changed
2024-08-26 iOS: PID gains bundled into a struct
2024-08-26 iOS: Simple PID position control and forward motion with orientation tracking (works poorly because small angles are still hard to correct)
2024-08-26 Server: Drive forward command (uses PID) and added position PID controller to PID gains command
2024-08-27 Hoverboard: Fixed message parsing
    [hoverboard.ino]
2024-09-09 iOS: Filter out low confidence values (slow)
2024-09-09 iOS: C++ filterDepthMap() function should be faster than Swift
2024-09-14 Server: Navigation UI: Refresh map and 360 scan buttons
2024-09-14 Parts: Camera mounts
    [Camera Mount - 0 Degrees.3mf, Camera Mount - 15 Degrees.3mf, Camera Mount 0.stl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]
2024-09-16 iOS: Added SwiftAnthropic package and WebRTCVAD framework
2024-09-18 Parts: Added extrusion end caps and reorganized directory
    [Camera Mount - 0 Degrees.3mf, Camera Mount - 0 Degrees.stl, Camera Mount - 15 Degrees.3mf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]
2024-09-20 Parts: Extrusion connector to join two extrusions together
    [Extrusion Connector.3mf, Extrusion Connector.stl]
2024-09-24 iOS: Procedure to follow person (not currently activated)
2024-09-30 Parts: Charging case
    [Case Bottom.3mf, Case Bottom.stl, Case Top.3mf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]
2024-10-01 iOS: AnnotatingCamera: Added annotation styles, namely a new headingAndDistanceGuides (currently not used)
2024-10-01 iOS: Annotation style is selectable in Brain and fixed bugs with current photo identification and map labeling
2024-10-02 iOS: ARSessionManager: Changes that should make frame subscribers receive frames simultaneously
2024-10-03 iOS: Record videos and save to photo library. Recording audio (speech) rarely works beyond the first sample.
2025-12-21 iOS: Manually truncate text at stop keywords, just in case

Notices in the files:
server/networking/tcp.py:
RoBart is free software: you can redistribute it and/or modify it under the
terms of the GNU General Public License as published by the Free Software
